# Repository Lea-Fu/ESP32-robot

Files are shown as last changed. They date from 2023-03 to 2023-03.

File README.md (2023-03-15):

# Autonomous tangible microrobots for app based (board) games

[Allgemein](#allgemein) <br>
[Tests](#tests) <br>
[Architekturüberlegung](#architekturüberlegung) <br>
[Implementierung](#implementierung) <br>
[Löten](#löten) <br>
[Steuerung](#steuerung) <br>
[Modellierung](#modellierung) <br>
[Display](#display) <br>
[Kamera](#kamera) <br>
[Nachrichten](#nachrichten) <br>
[App](#app) <br>
[Aruco Generation](#arucogeneration) <br>
[Ausblick](#ausblick) <br>

**Roboter:**
besteht aus: 
- ESP32(Wifi und Bluetooth) mit Kamera
- OLED Display
- H Brücke
- 2 Motoren N20 (2-4V 145RPM)
- Akku 3,7V 800mAh lipo
- 4 3D gedruckten Rädern
- 3D gedrucktes Getriebe
- 3D gedrucktes Gehäuse

**Gearbeitet wurde mit:**
- Für die **App**: Android Studio -> **Java**
- Für den **Roboter**: **PlatformIO** -> Arduino -> CLion -> **C++**
- Für die **Bildverarbeitung**: Computervision Bibliothek für ArUco Marker -> **OpenCV**
- Für das **Spielfeld**: um ein ArUco Board zu generieren -> OpenCV und **Python**
- Für die **Konstruktion** des Roboters: um die 3D Teile für den Roboter zu drucken -> **Fusion360** und **3D Drucker**

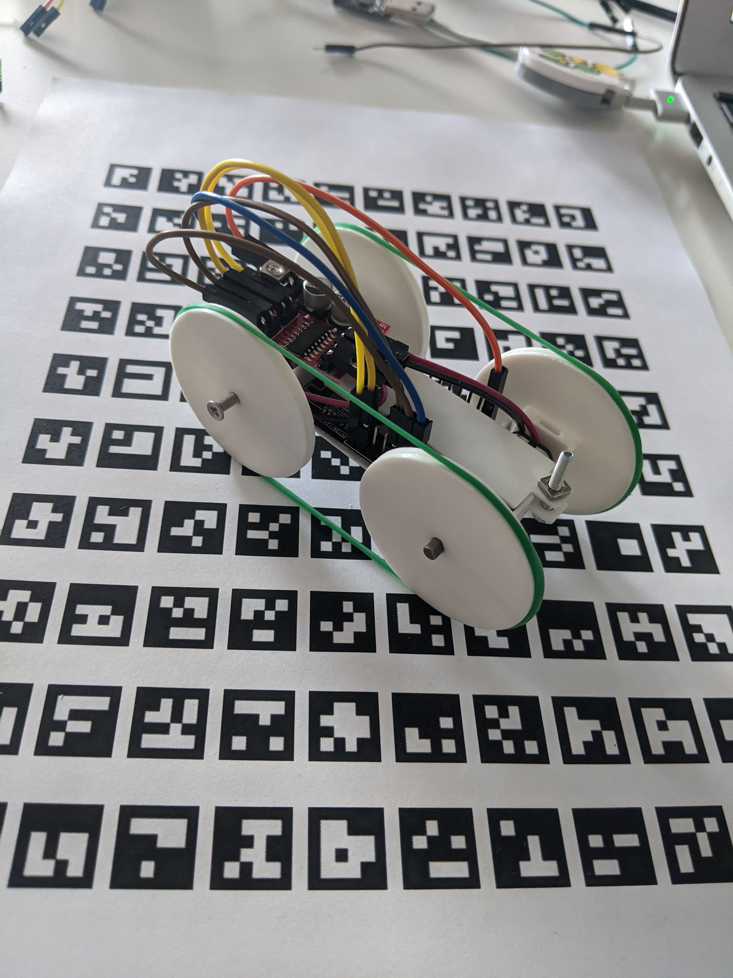
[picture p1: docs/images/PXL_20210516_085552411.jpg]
image of robot


App Icon (ganz oben links sieht man den Icon der App):
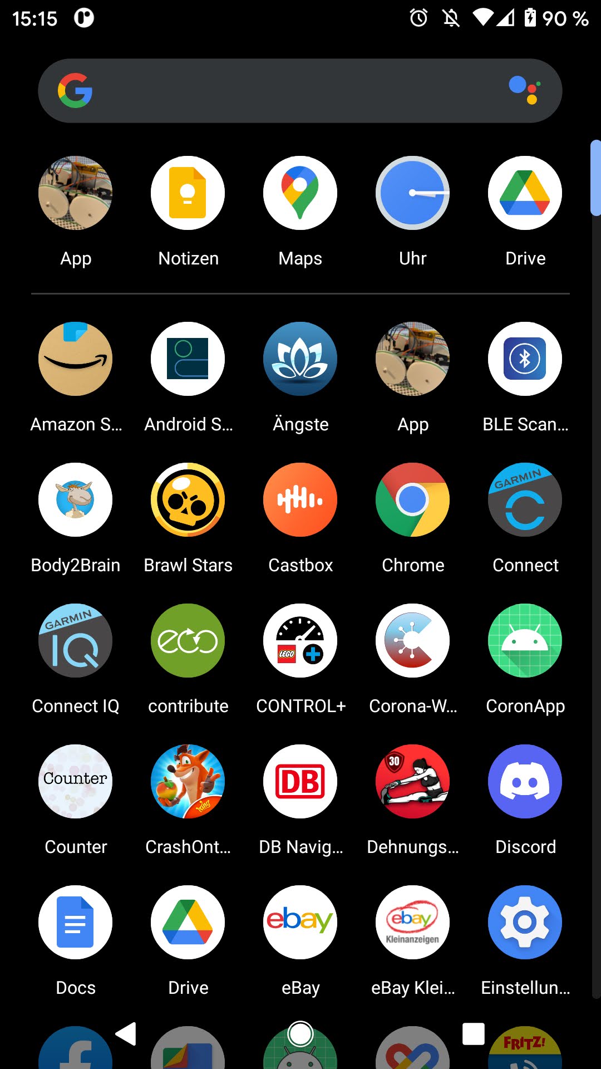
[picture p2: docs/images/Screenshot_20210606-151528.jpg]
image of app icon


## Erste Tests des ESP32

Nach Ankunft des **ESP32** mit Kamera testeten wir ihn, indem wir in **CLion** das Plugin für **PlatformIO** installierten. Um in CLion mit **Arduino** und dem esp32cam board arbeiten zu können, muss es unter  AI Thinker ausgewählt werden.

Das erste kleine Testprojekt besteht aus drei Teilen.
1. Ausgabe von "Hello" auf der Commandozeile
2. Anzeigen der verfügbaren WLAN Netzwerke
3. Möglichkeit des verbindens mit Bluetooth

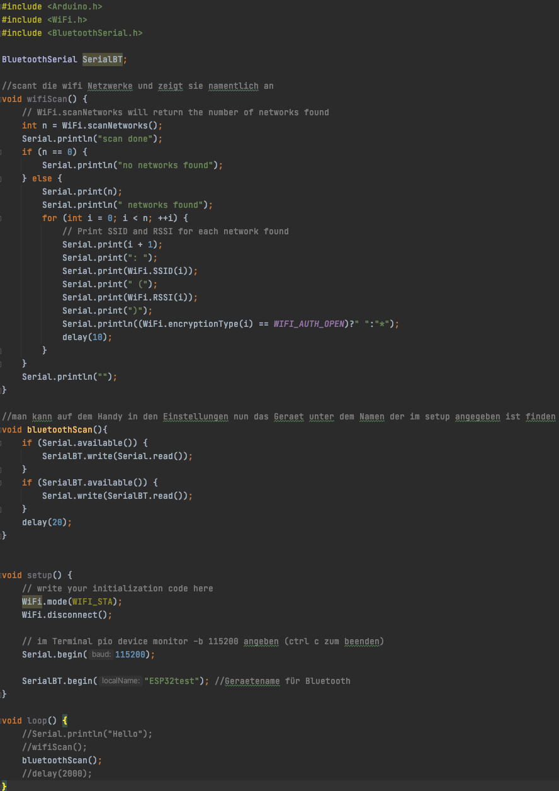
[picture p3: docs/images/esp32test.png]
esp32test code sample


## Architekturüberlegung

Sehr abstrakt gesehen:

architecturAbstrakt

Lose Kopplung -> hoher innerer Zusammenhalt und trennen der Zuständigkeiten

alles spezielle wegkapseln, damit es leicht austauschbar ist!

Erste Überlegungen zur "genauen" Architektur:

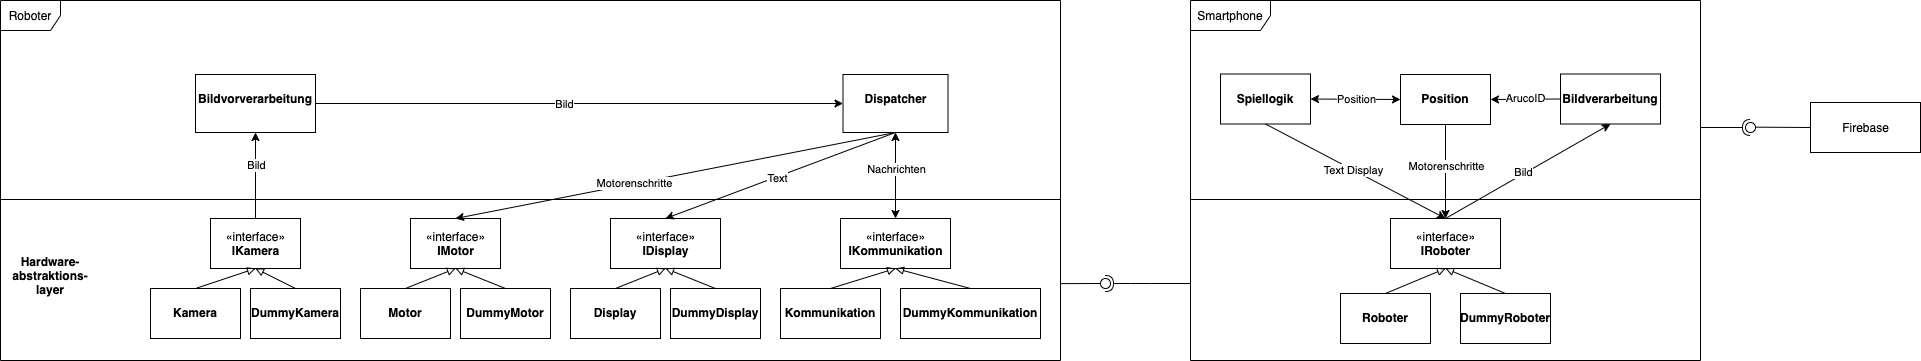
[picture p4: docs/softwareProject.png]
softwareProject


Auf der Seite der App war die Architekturüberlegung die im Diagramm zu sehen ist noch nicht genau genug und wurde deshalb nicht komplett übernommen. Auf Seite des Roboters hat es bis zum Ende hin gepasst und die Architektur vom Anfang wurde übernommen.

Für die Klasse dispatcher auf dem Roboter:

| Komponente | Feld 0 | Feld 1 |
| --- | --- | --- |
| Format | Header 1 Byte Adresse für HAL Komponenten | Nachricht |
| Kamera | '0' | ‘0‘ für senden der graustufen Bilder ‘1‘ für stop |
| Motor1 | '1' | message[1]'1' oder '0' für Vorwärts oder Rückwärts, oder '2' für stop, als String, alles andere um nichts zu tun |
| Motor2 | '1' | message[2]'1' oder '0' für Vorwärts oder Rückwärts, oder '2' für stop, als String, alles andere um nichts zu tun |
| Display | '3' | Text als String |

## Implementierung für den Roboter

Es wurde sich als Konvention für "snake case" entschieden. Also alles wird mit Unterstrichen (_) getrennt.

Die Klassen sind, wie unter [Architekturüberlegung](#architekturüberlegung) festgehalten, eingeteilt. Zu jeder .cpp File gibt es eine passende .h File. Die Header liegen alle im "include" Ordner. In diesem befindet sich der Unterordner "hal", dies steht für HardwareAbstraktionsLayer. Die Source Files liegen alle im "src" Ordner und auch hier gibt es den Unterordner "hal".
"i" am Anfang eines Klassennamen deutet auf ein Interface hin.

Struktur:
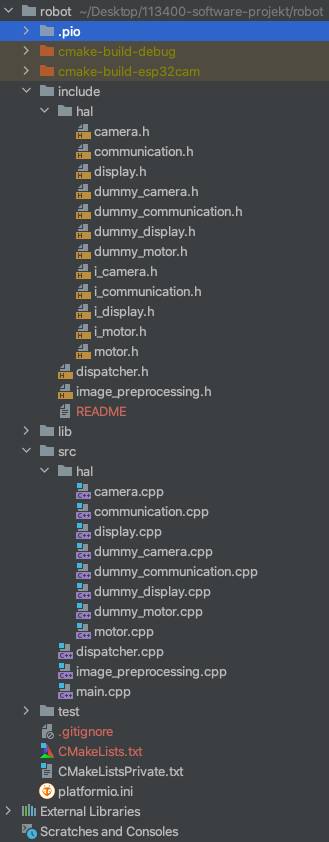
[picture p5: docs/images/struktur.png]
struktur


1. Zuerst wurde die WLAN und Bluetooth Funktionalität aus den ersten Tests des ESPs hier in die communication eingebunden.
2. Als nächstes wurde start und stop für den Motor implementiert. Siehe unter [Steuerung](#steuerung)
3. Dann wurde der dispatcher für das senden und empfangen von Nachrichten implementiert.
4. Implementierung für das Display zum Anzeigen von Nachrichten. Siehe unter [Display](#display)
5. Die Kamera kann nun ein Foto aufnehmen. Siehe unter [Kamera](#kamera)
6. Nachrichten über BLE (Bluetooth Low Energy) senden. Problem: wir bekommen mit einem normalen Netzteil 4,7 V und das reicht nicht. Also der Brownout detector springt an, da es einen Spannungsabfall gibt. Lösung: Kondensator reicht nicht, also stärkeres Netzteil. Selbst 9,6 V haben nicht funktioniert. Also haben wir einfach einen neuen ESP32 benutzt. Es ging sofort, nur mit dem Strom des Laptops ohne Probleme. Siehe unter [Nachrichten](#nachrichten)
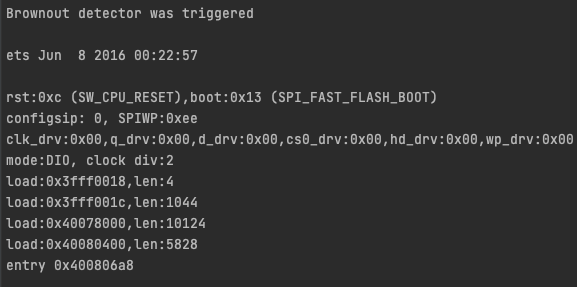
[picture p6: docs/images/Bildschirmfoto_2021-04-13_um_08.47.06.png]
Bildschirmfoto_2021-04-13_um_08.47.06


7. über BLE ein Bild vom ESP32 an die inzwischen selbst geschriebene App schicken. Problem: Bild ist 9,216KB groß, ESP sendet nur bis 0,6KB. Lösung: Paket in Packages aufteilen und rüberschicken.
8. das Bild enthält einen Marker der mittels OpenCV erkannt wird. So weiß der Roboter wo er ist und wo er hin muss.

## Löten von Motoren und H Brücke

Zuerst braucht man den Lötkolben, eine dritte Hand, Lötzinn, Kabel, Motoren und die H-Brücke.
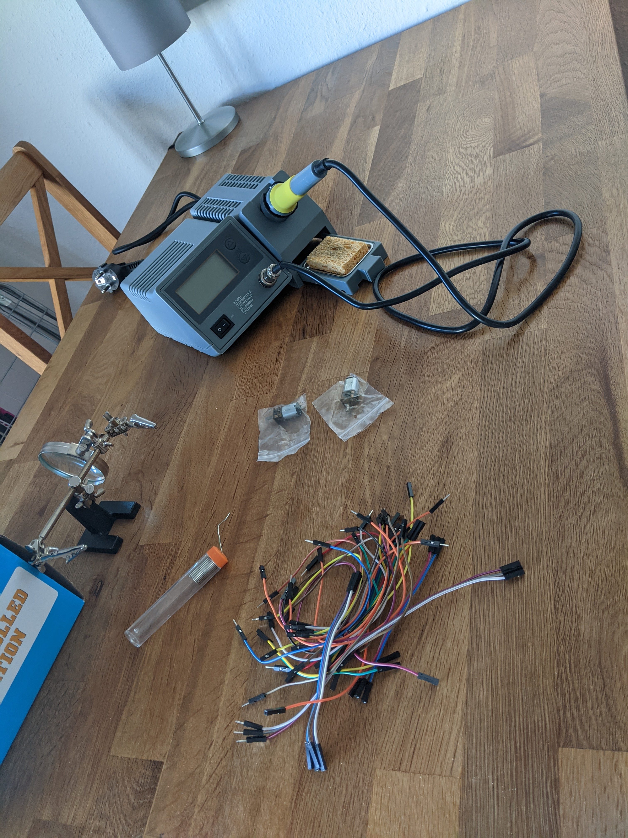
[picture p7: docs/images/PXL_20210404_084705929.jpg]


Dann nimmt man sich zwei Motoren und 2 Kabel (female auf beiden Seiten).
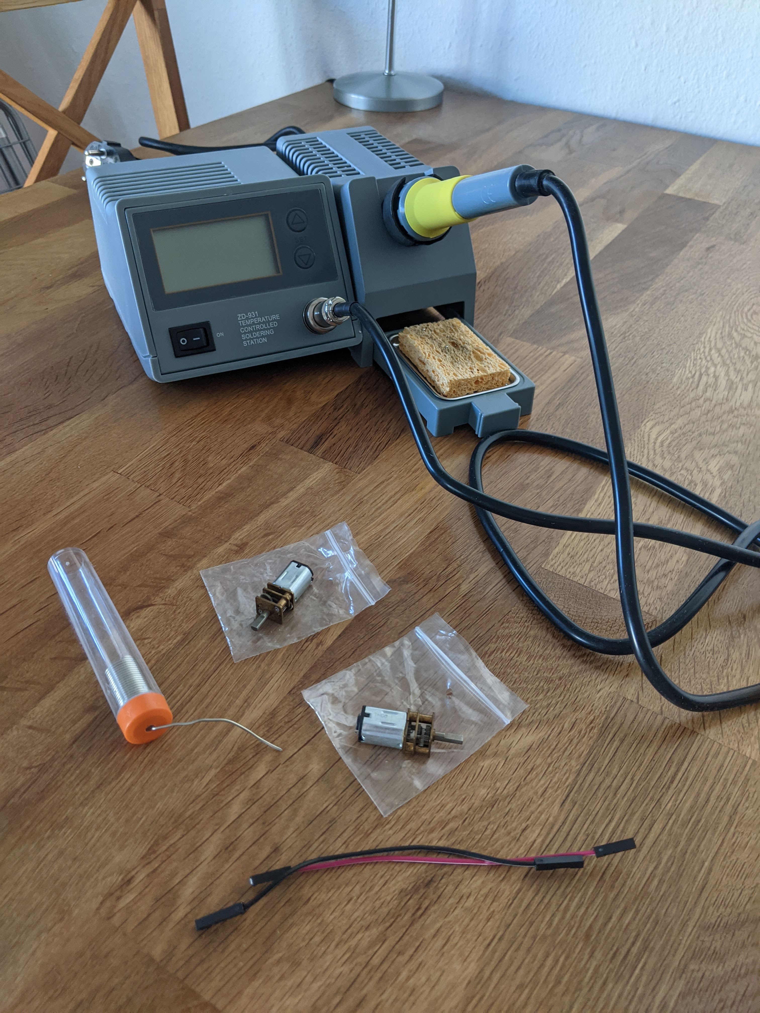
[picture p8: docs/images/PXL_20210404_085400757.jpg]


Nun trennt man beide Kabel genau in der Mitte und entfernt die Isolierung vorsichtig.
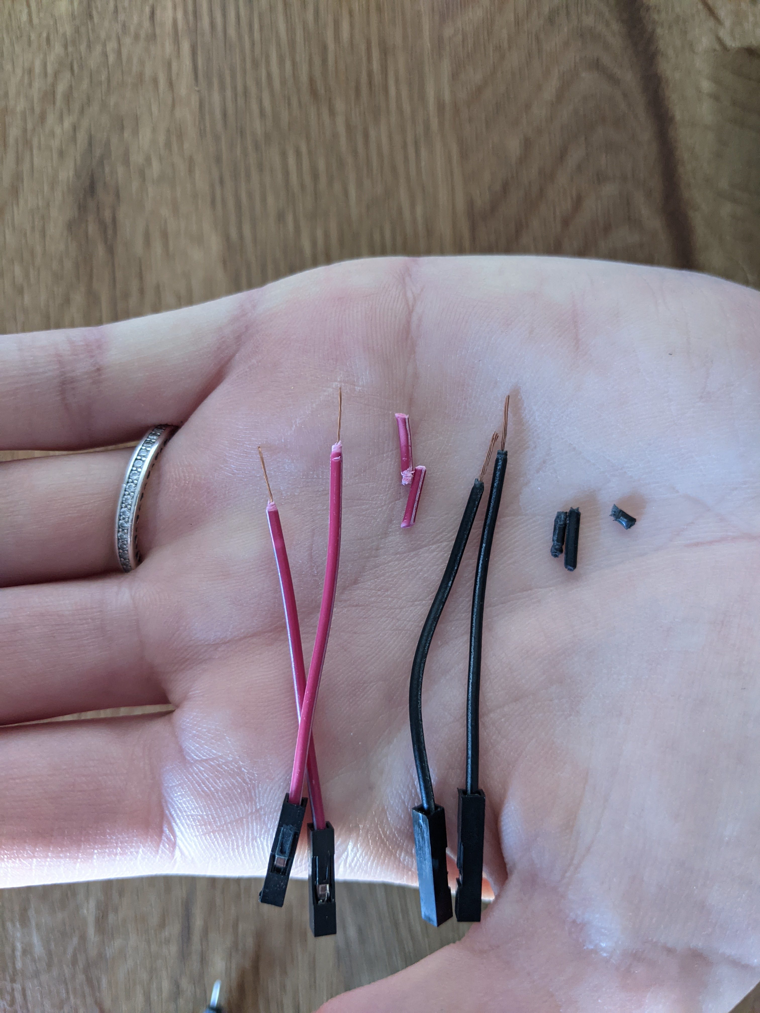
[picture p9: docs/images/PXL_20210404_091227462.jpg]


Wir haben uns für rot als Plus- und schwarz als Minus-Kabel entschieden. Die Kabel können nun an die Motoren gelötet werden.
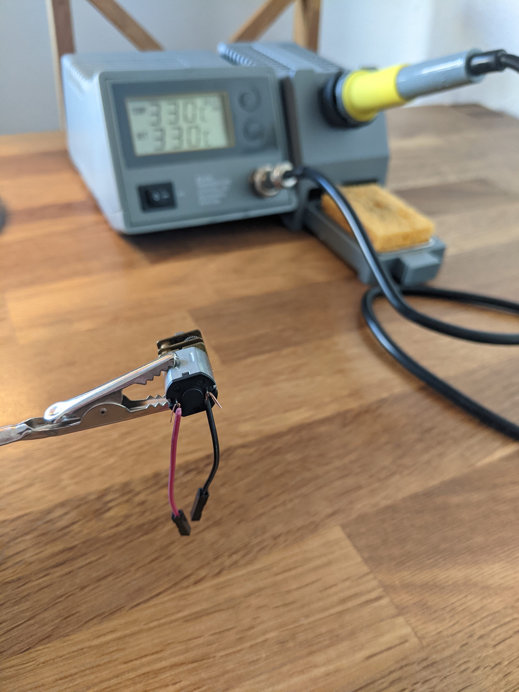
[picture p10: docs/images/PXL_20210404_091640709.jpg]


Man kann den Motor nun mit rot an 3,3V und mit schwarz an G für Ground des ESP stecken. Dies haben wir zum testen gemacht. Wenn man den ESP nun mit der Steckdose verbindet, läuft der Motor.
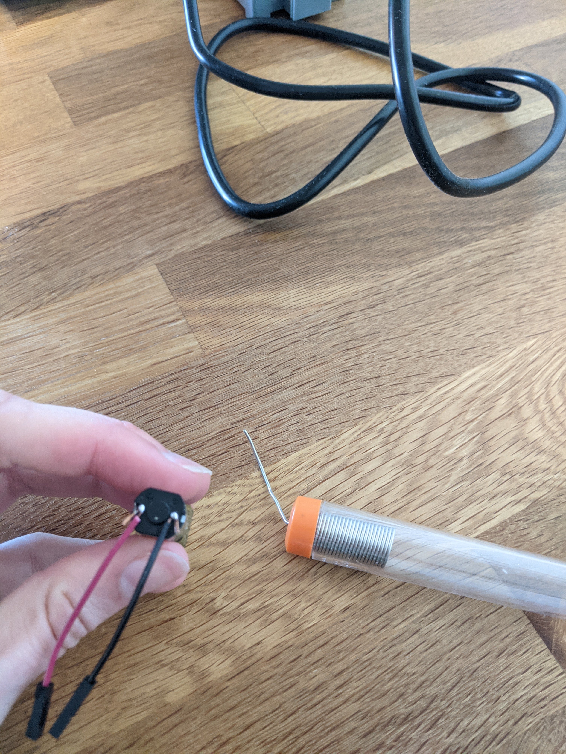
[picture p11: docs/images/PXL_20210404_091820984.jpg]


Dann trennt man immer zwei Kontaktstifte von der Stiftleiste ab. 5 Paare werden für eine H-Brücke gebraucht.
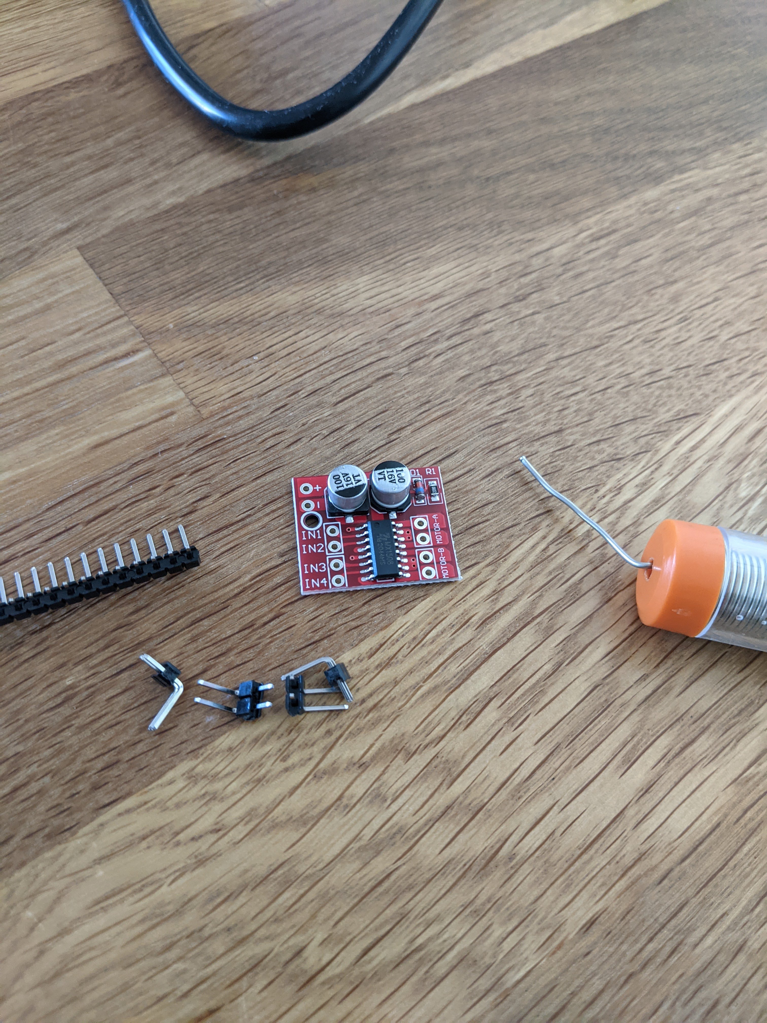
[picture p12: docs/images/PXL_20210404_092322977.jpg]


Diese lötet man nun fest.
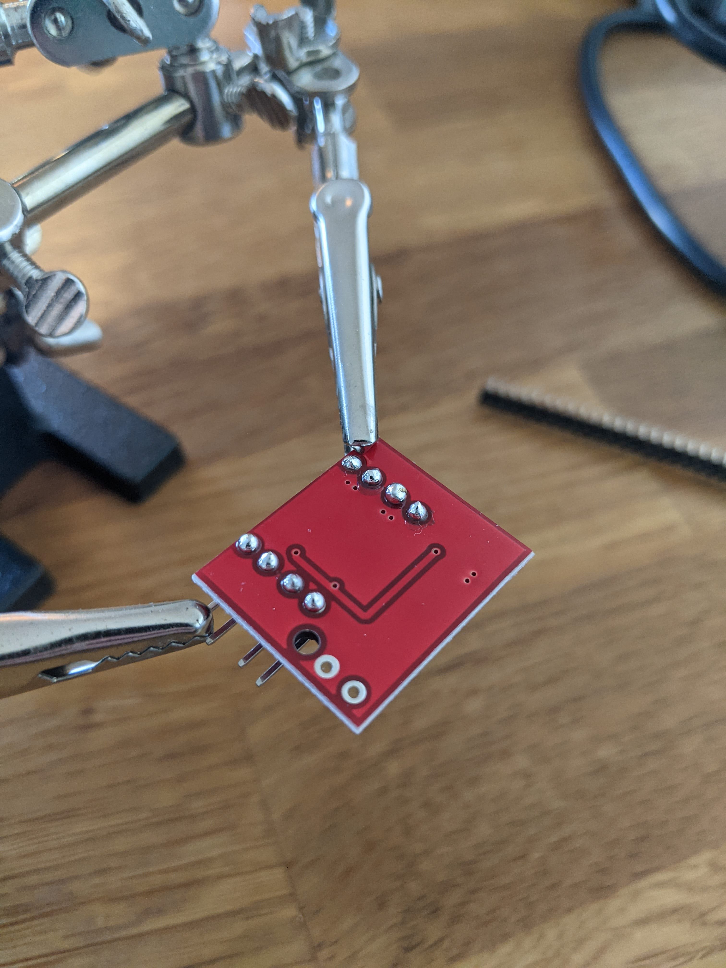
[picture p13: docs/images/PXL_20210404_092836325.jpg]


Hier sind alle festgelötet.
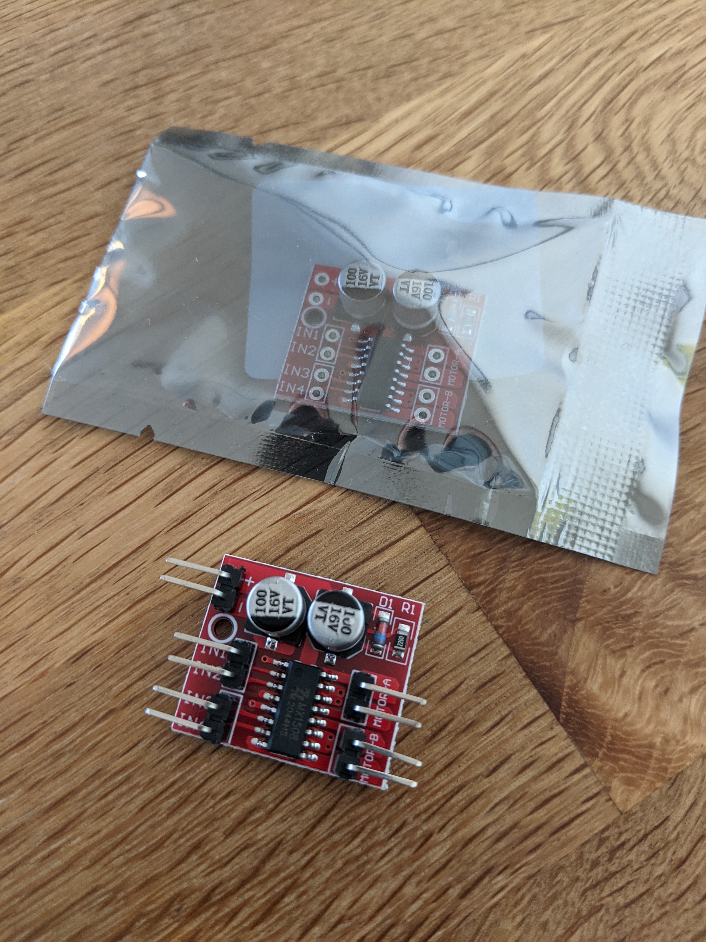
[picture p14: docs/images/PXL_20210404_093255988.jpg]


Man kann die Motoren nun an Motor A und Motor B der H-Brücke befestigen.
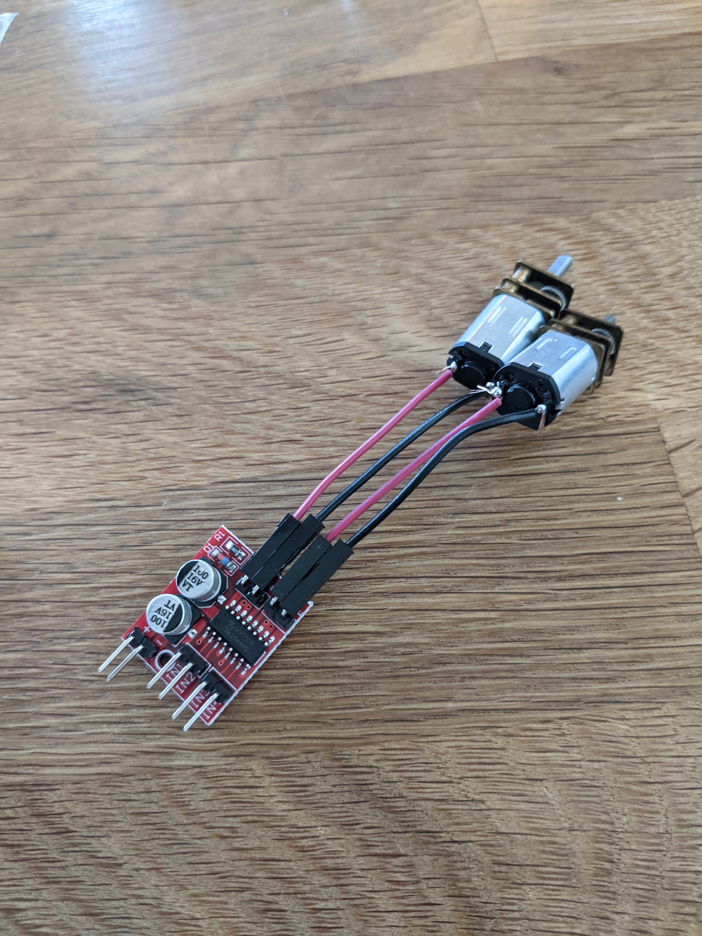
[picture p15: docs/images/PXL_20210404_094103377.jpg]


## Motoren ansteuern

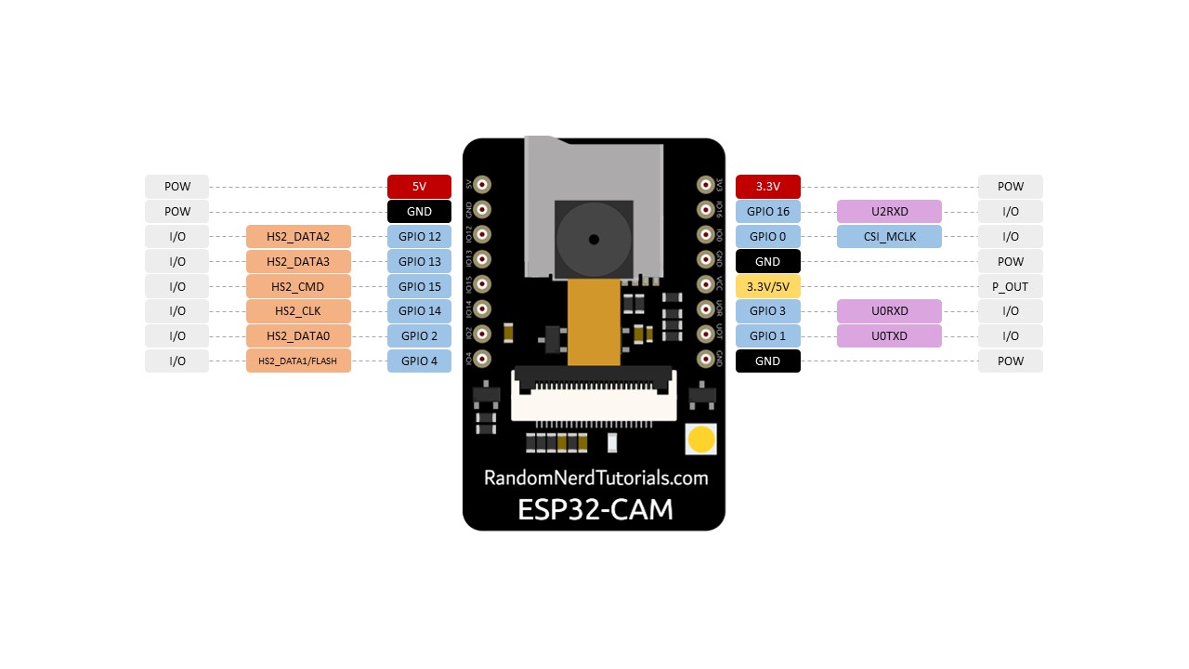
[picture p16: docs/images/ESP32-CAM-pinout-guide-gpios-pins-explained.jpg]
ESP32-CAM-pinout-guide-gpios-pins-explained


Um zu gucken, welche Pins des ESP32 auf welche in Arduino gemappt sind.

https://randomnerdtutorials.com/esp32-cam-ai-thinker-pinout/

Aufbau zum Testen:

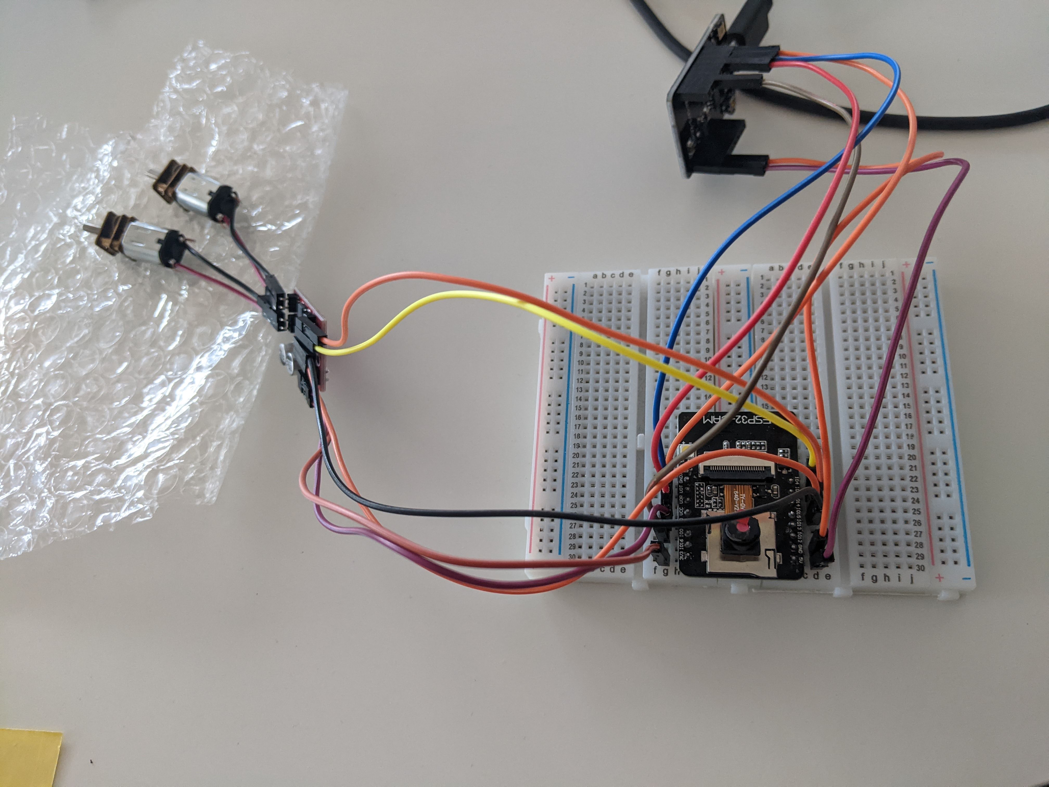
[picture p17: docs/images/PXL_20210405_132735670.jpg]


Die beiden Motoren werden an die H-Brücke angeschlossen.
Die H-Brücke wird mit Motor A an IO13 und IO12 angeschlossen. Motor B wird an IO4 und IO2 angeschlossen. Plus der H-Brücke wird an 3,3V und Minus der H-Brücke an GRN (Ground).
5V des ESP32 wird an 5V des Adapters für den Strom angeschlossen und GND (Ground) des ESP32 wird an GND (Ground) des Adapters für den Strom angeschlossen.

Zusätzlich habe ich noch IO0, UOR, UOT, GND/R an die jeweiligen Pins des Adapter angeschlossen, um den Code uploaden zu können, ohne des ESP32 von der Steckplatte nehmen zu müssen.

IO4 musste gegen IO14 ersetzt werden, da die LED an IO4 hängt und somit immer an geht, wenn man den Motor anspricht. Da wir nun PVM für die Motoren benutzen, um die Geschwindigkeit zu steuern, flackert die LED, so können die Marker nicht mehr erkannt werden. Deswegen musste der Pin gewechselt werden, das bedeutet aber auch, das nicht genug freie Pins für das Display vorhanden ist und dies wegfallen muss.

## Modellierung in Fusion360

Der Roboter wird in Fusion360 modelliert, um die Basis und die Räder 3D Drucken zu können.

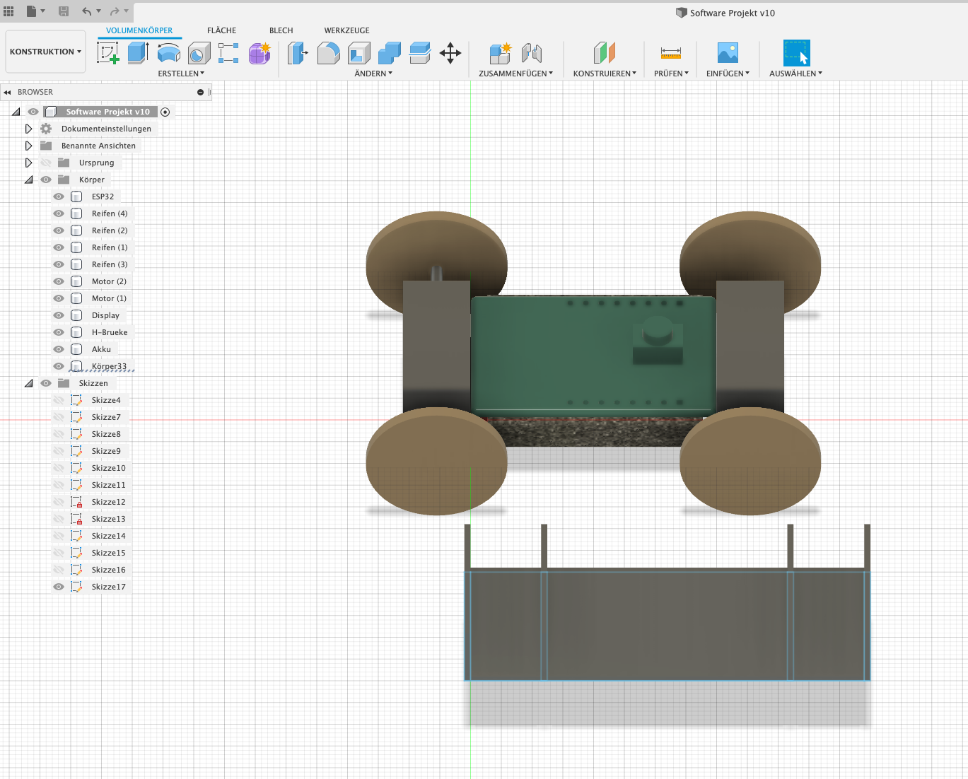
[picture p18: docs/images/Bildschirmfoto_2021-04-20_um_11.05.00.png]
Bildschirmfoto_2021-04-20_um_11.05.00


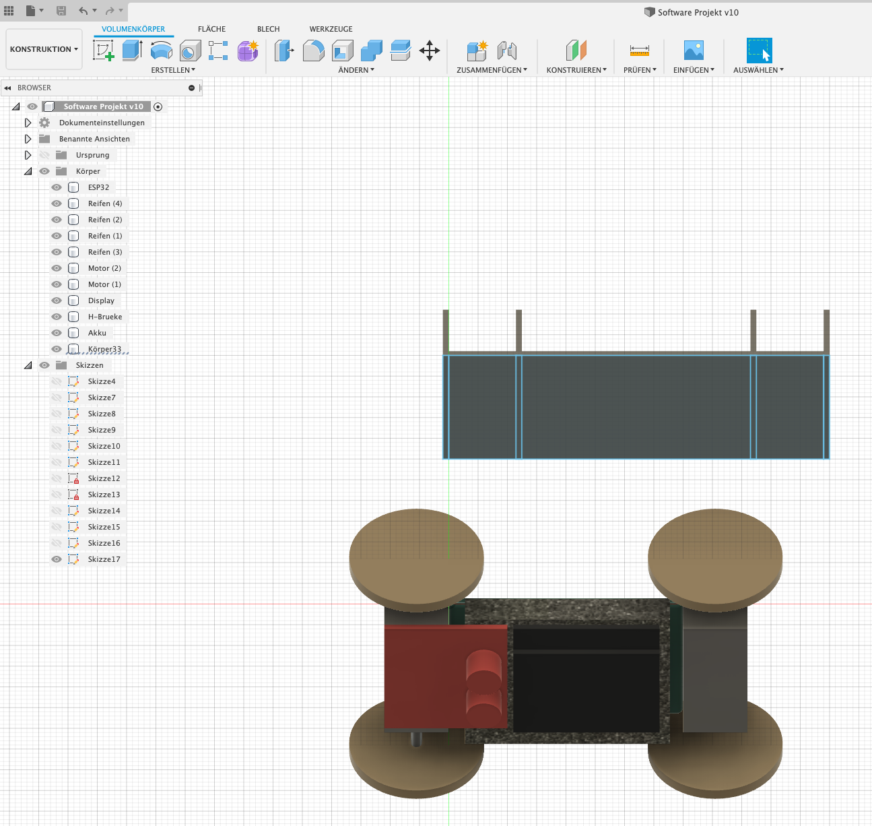
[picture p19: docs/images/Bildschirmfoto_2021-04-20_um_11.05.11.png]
Bildschirmfoto_2021-04-20_um_11.05.11


Hier sieht man erste Prototypen.

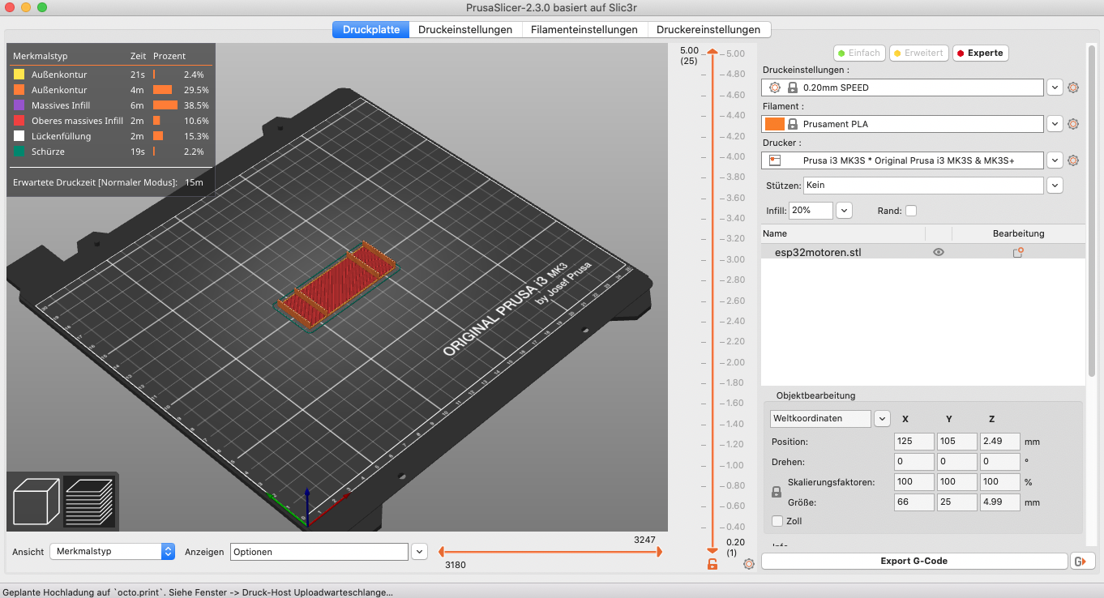
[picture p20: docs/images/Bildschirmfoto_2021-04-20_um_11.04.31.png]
Bildschirmfoto_2021-04-20_um_11.04.31


Dies ist der erste Testdruck für die Halterung des ESP32 und der Motoren, die rechts und links daneben kommen.

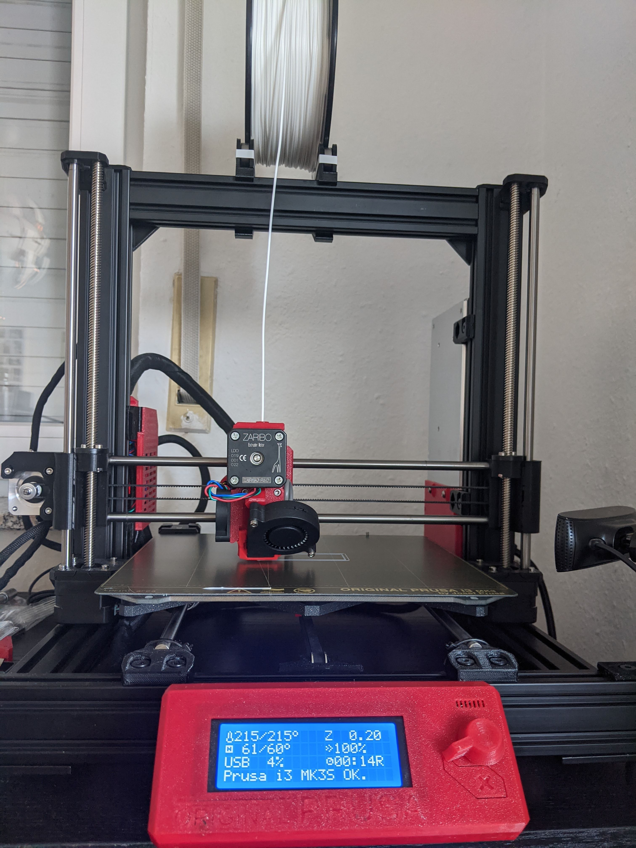
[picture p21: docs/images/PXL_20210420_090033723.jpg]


Hier der erste fertige Testdruck. Die Toleranzen werden nun weiter überarbeitet, bis es perfekt passt.

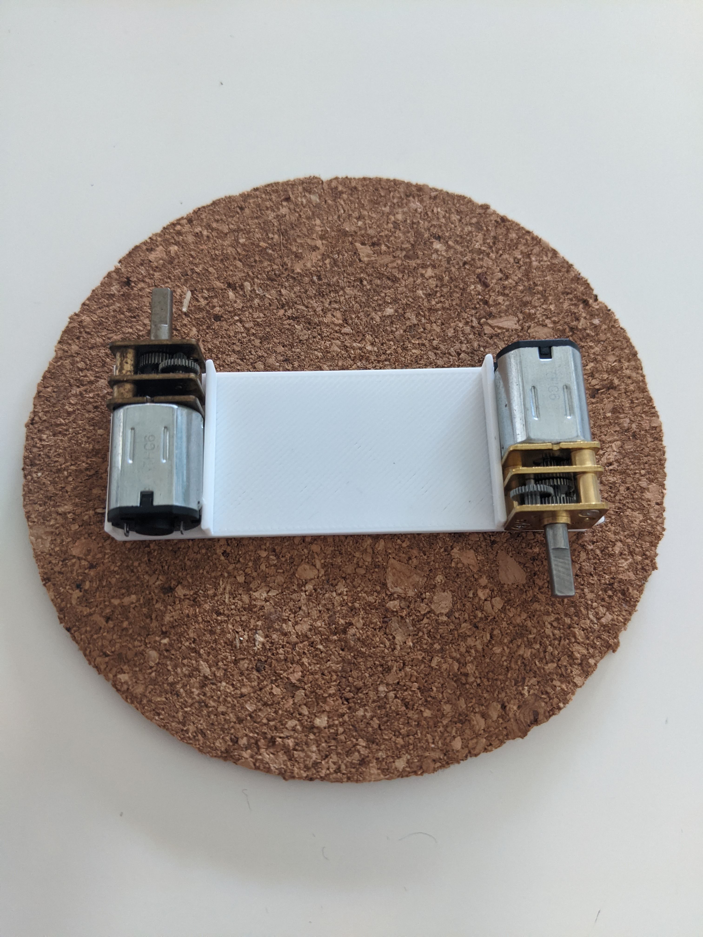
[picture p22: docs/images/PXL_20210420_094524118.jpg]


Der Wendepunkt liegt genau in der Mitte, damit ist der **Roboter** im Gegensatz zu einem Auto **Holonom** und kann sich **auf der Stelle drehen**, indem ein Motor vorwärts, der andere rückwärts fährt.

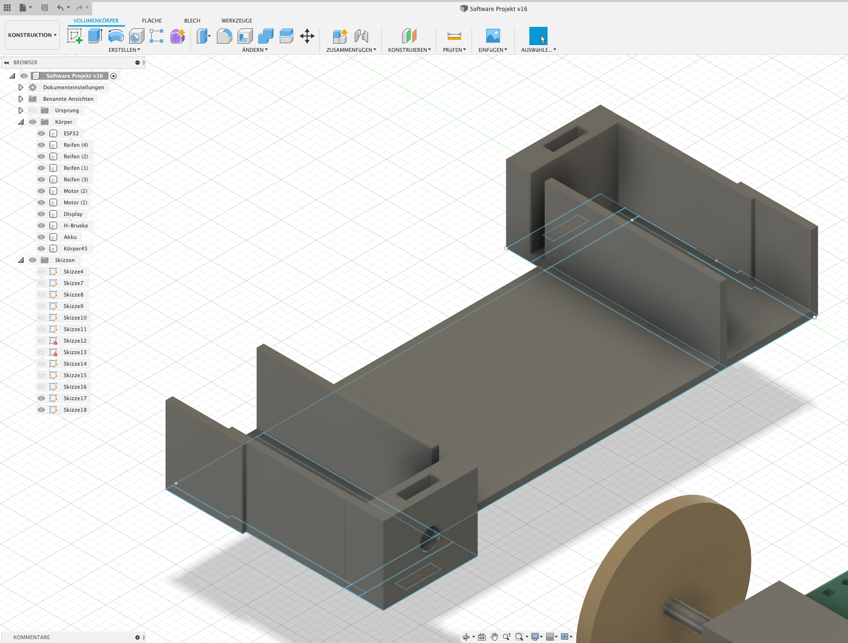
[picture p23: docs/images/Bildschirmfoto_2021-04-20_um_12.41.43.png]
Bildschirmfoto_2021-04-20_um_12.41.43


Hier sind hinter den Motoren nun Wände, zwischen diesen müssen die Kabel langgehen und in den Wänden ist Platz für eine M2,5 4Kant Mutter. In die kommt eine Schraube M2,5 x 12, an diese soll dann das Rad.

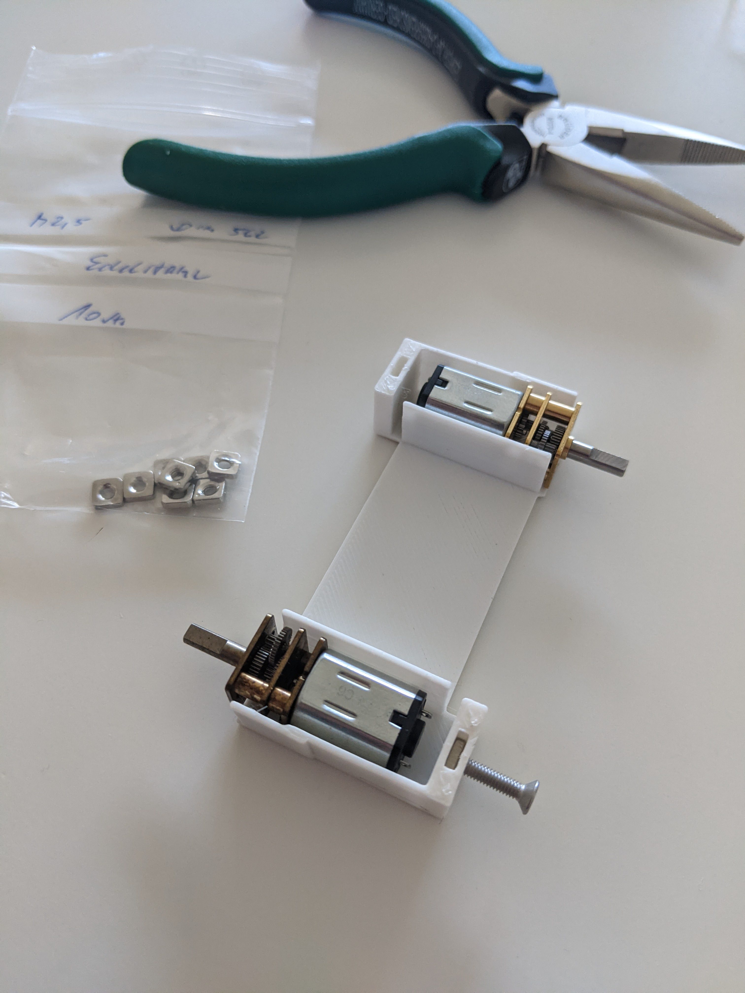
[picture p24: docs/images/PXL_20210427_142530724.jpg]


Hier sind die zwei Motoren und der Esp32 cam verbaut. Es fehlt also oben noch der Akku, das Display und die H-Brücke muss auch noch drauf.

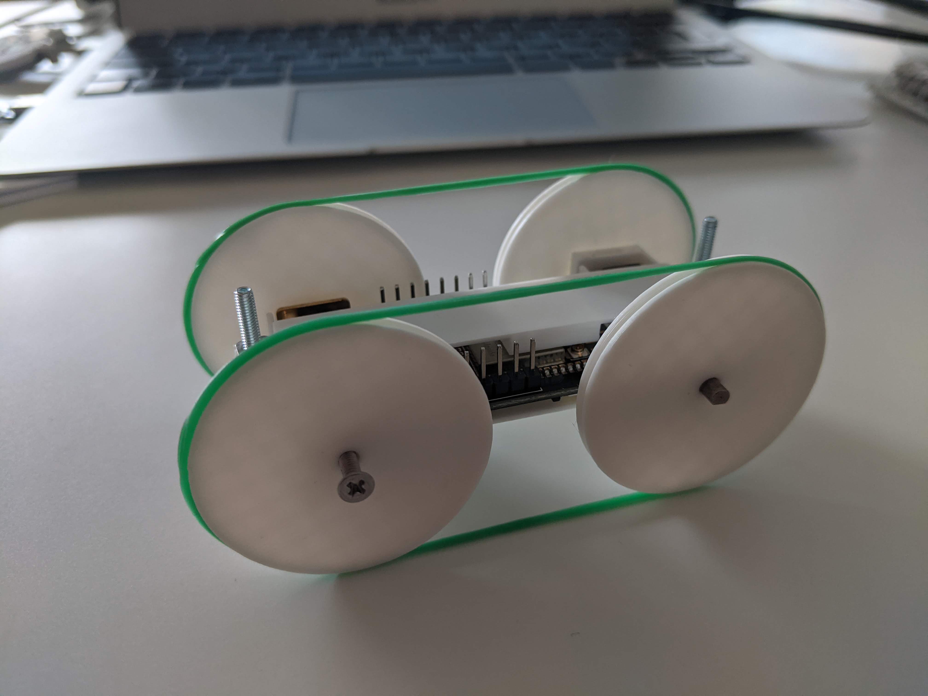
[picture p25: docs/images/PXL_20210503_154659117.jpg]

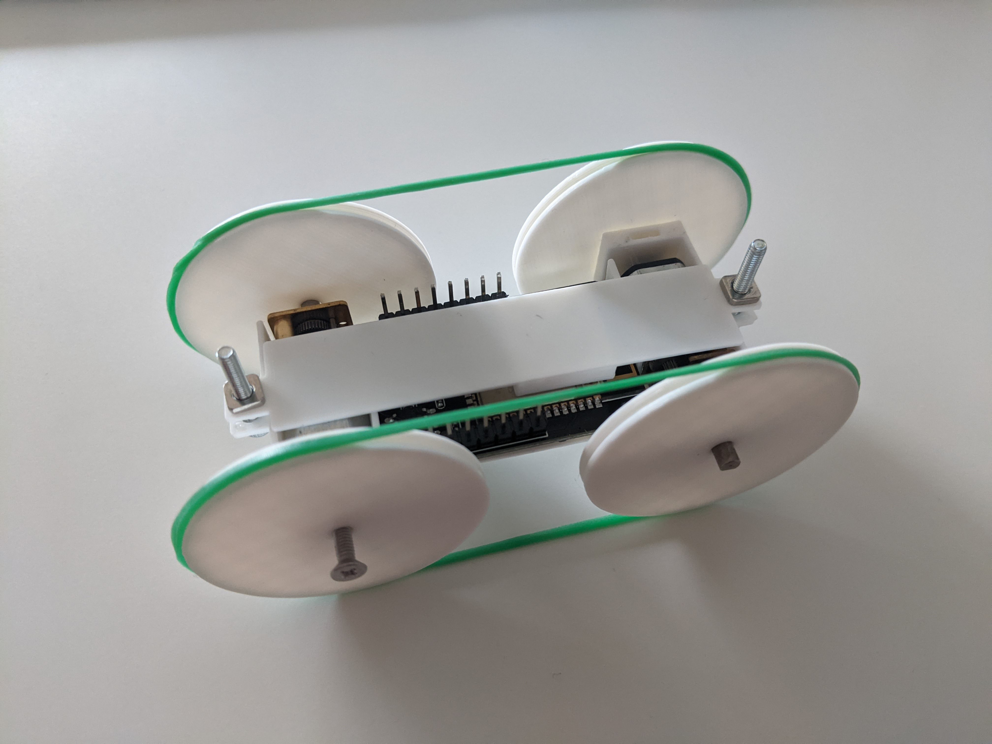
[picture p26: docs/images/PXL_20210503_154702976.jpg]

Auf dem folgenden Bild sieht man den Robo von unten. Hier sieht man die Kamera, die die ArUco Marker auf den Feldern erkennt. Wir benutzen sie, damit wir wissen, auf welchem Feld wir stehen (Marker ID -> x und y Koordinate) und wie wir allgemein stehen (Pose estimation -> Translation und Rotation zum Marker):
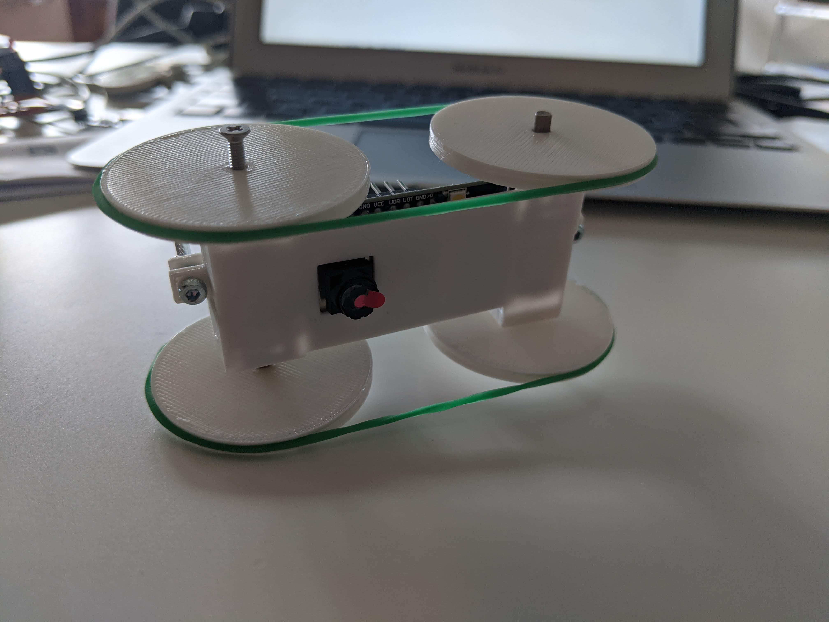
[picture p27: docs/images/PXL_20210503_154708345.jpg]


Der Roboter zusammengebaut:


Drucken größerer Reifen:
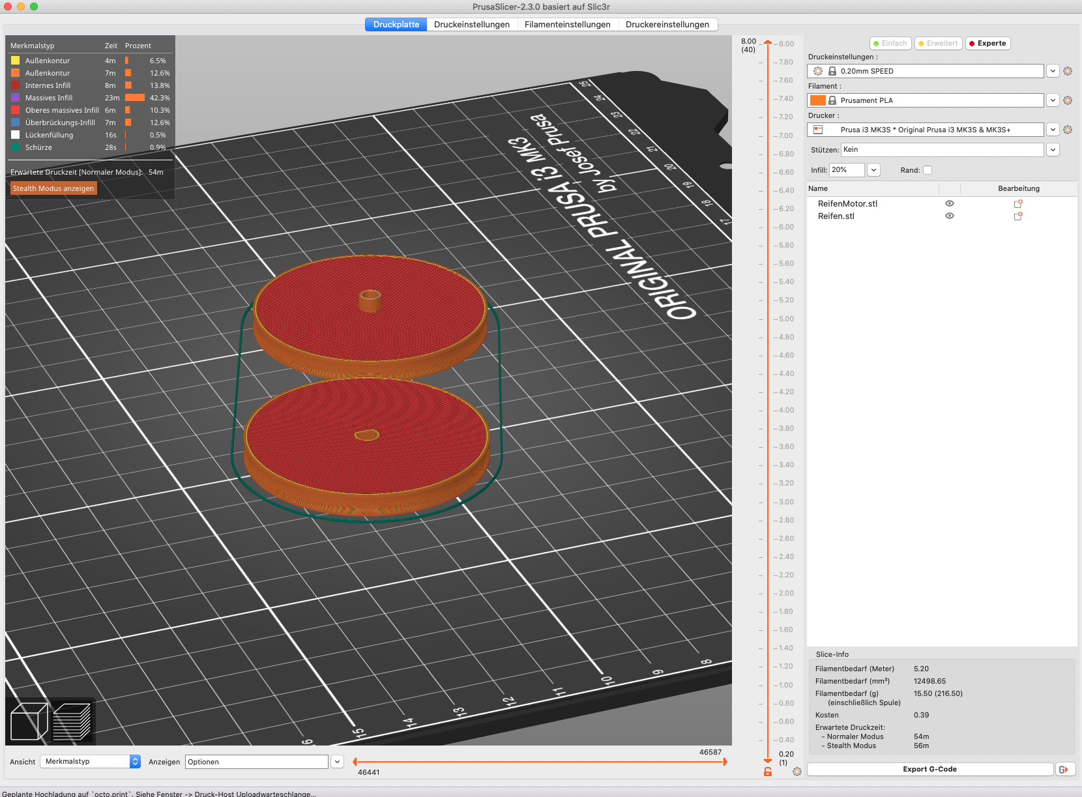
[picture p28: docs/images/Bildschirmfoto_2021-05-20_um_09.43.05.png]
Bildschirmfoto_2021-05-20_um_09.43.05


Um den Roboter zusammenzubauen braucht man die .stl Files aus dem Repo. Sie liegen auf dem Master Branch unter docs/CAD.

## Display testen

Bibliothek für das Display: 
https://platformio.org/lib/show/135/Adafruit%20SSD1306/examples
https://platformio.org/lib/show/6214/Adafruit%20BusIO/installation

Das Display hat GND, das muss an GND vom ESP32 angeschlossen werden. 
VCC vom Display wird an 3,3V vom ESP32 angeschlossen. 
SCL wird an IO15 und SDA an IO14 angeschlossen.

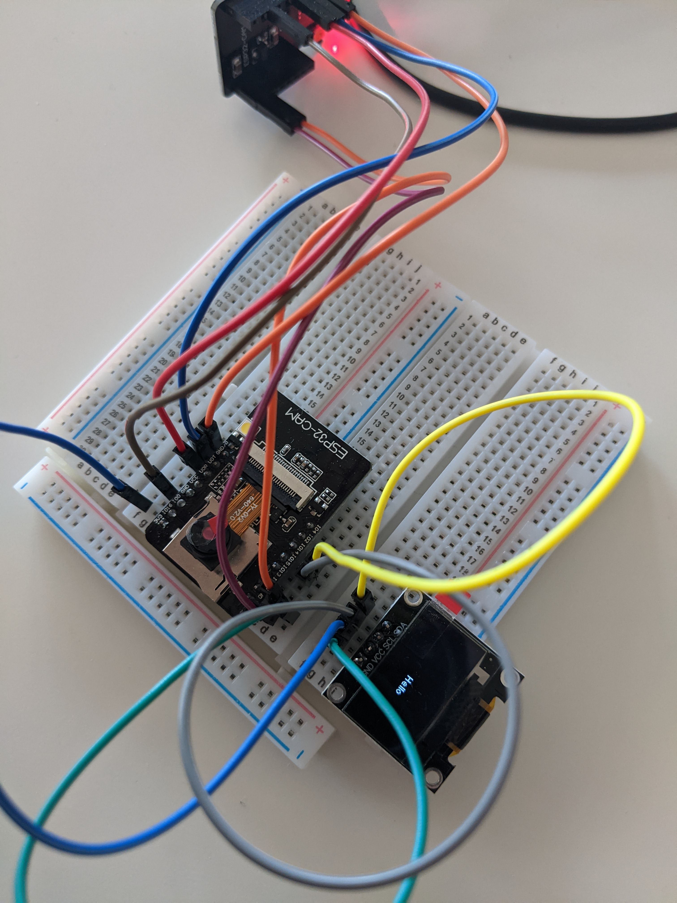
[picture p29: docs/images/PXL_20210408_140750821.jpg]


Das Display konnte im fertigen Projekt nicht mehr integriert werden, da der ESP zu wenige Pins besitzt. Dem Motor mussten leider ein Display Pin geben werden, wegen der LED des ESP. Mehr dazu siehe [steuerung](#steuerung).

## Kamera testen

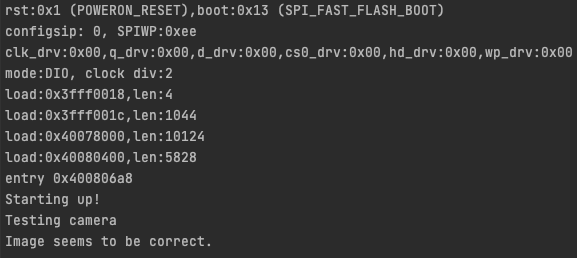
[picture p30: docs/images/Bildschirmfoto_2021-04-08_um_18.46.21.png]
Bildschirmfoto_2021-04-08_um_18.46.21


Unter dem Punkt die App kann man sehen, das die aufgenommenen Bilder 9,216 KB groß sind. Diese werden in 19 Paketen vom ESP32 zur App gesendet.

Mit der Nachricht "00" fängt er an Bilder zu senden. So schnell er kann. Es sieht aus, wie ein flüssiges Video. Mit "01" stoppt man das ganze.

## Nachrichten senden

Man kann auf dem Handy eine App namens BLE Scanner installieren. Dort kann man sich mit dem ESP32 verbinden und eine Nachricht senden. Diese kann man dann im Terminal von C Lion sehen, wenn man "pio device monitor -b 115200" eingibt.

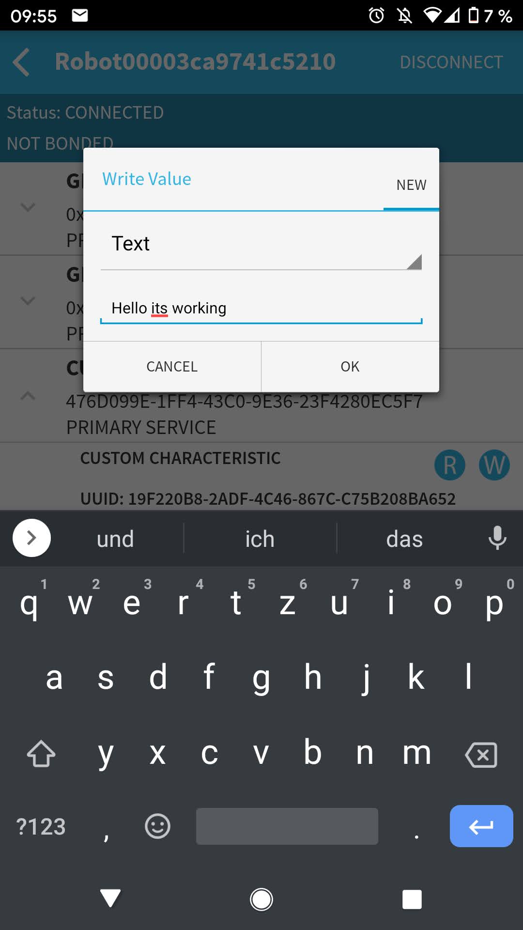
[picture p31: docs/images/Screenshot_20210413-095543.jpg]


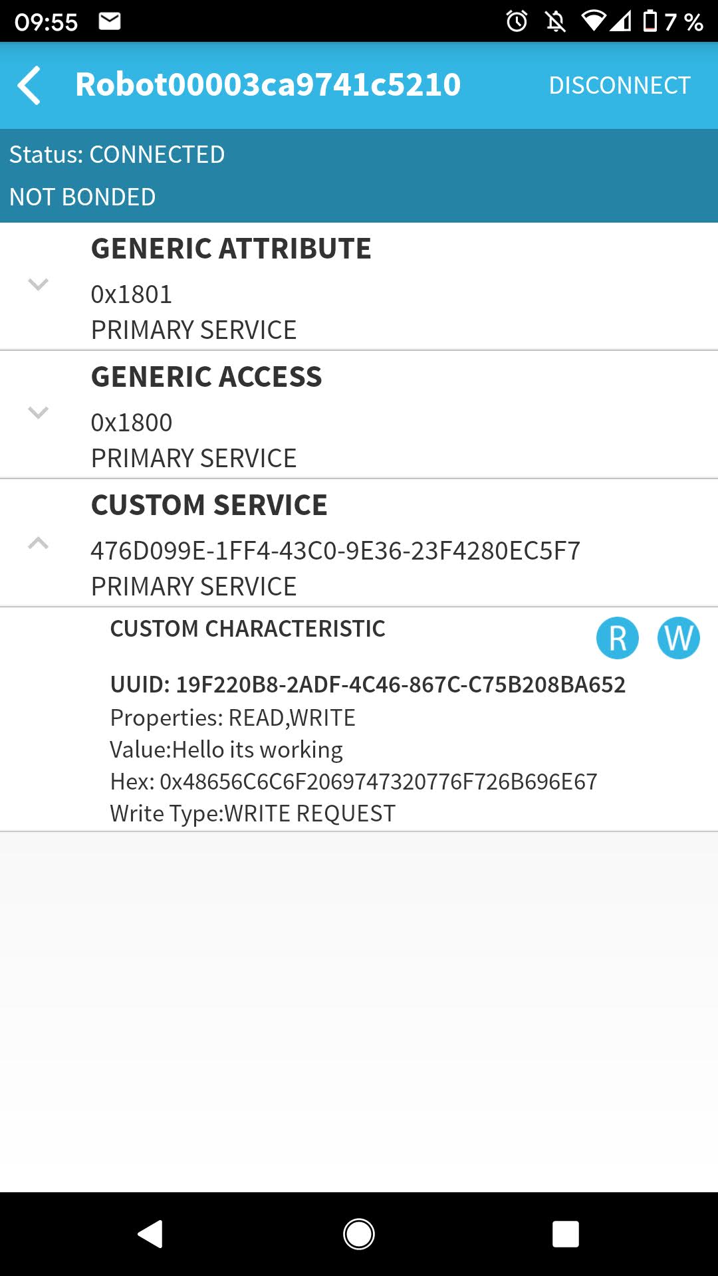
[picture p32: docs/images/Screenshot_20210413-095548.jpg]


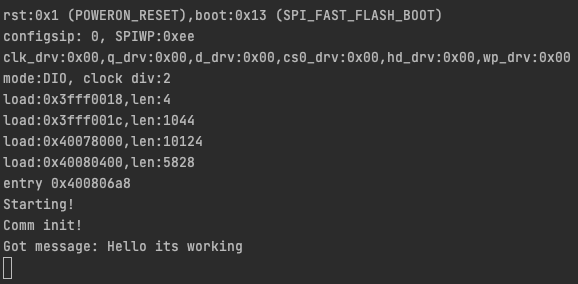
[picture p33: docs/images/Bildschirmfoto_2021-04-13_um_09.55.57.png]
Bildschirmfoto_2021-04-13_um_09.55.57


## Die App

OpenCV 4.5.2 mit contribs!!! für Android Studio: 

https://pullrequest.opencv.org/buildbot/export/opencv_releases/master-contrib_pack-contrib-android/20210425-042121--11332/

https://stackoverflow.com/questions/17767557/how-to-use-opencv-in-using-gradle

https://docs.opencv.org/2.4/doc/tutorials/introduction/android_binary_package/O4A_SDK.html

Wichtig:
https://stackoverflow.com/questions/57698796/cannot-detect-opencv-libs-after-update-form-3-4-3-to-4-1-1

Anfänglich:
1. Momentan kann man mit der App (auf dem Dev Branch Unterordner phone) über BLE mit dem Robo (ESP32) kommunizieren.
2. OpenCV ist über die oberen beiden Links mit eingebunden. Mit OpenCV können wir die ArUco Marker per Kamera erkennen.

https://docs.opencv.org/3.4.3/d5/dae/tutorial_aruco_detection.html

Hier wurde auf Papier der ArUco Marker mit der Id 7 ausgedruckt und vor die Kamera gehalten. Der Marker wird erkannt!

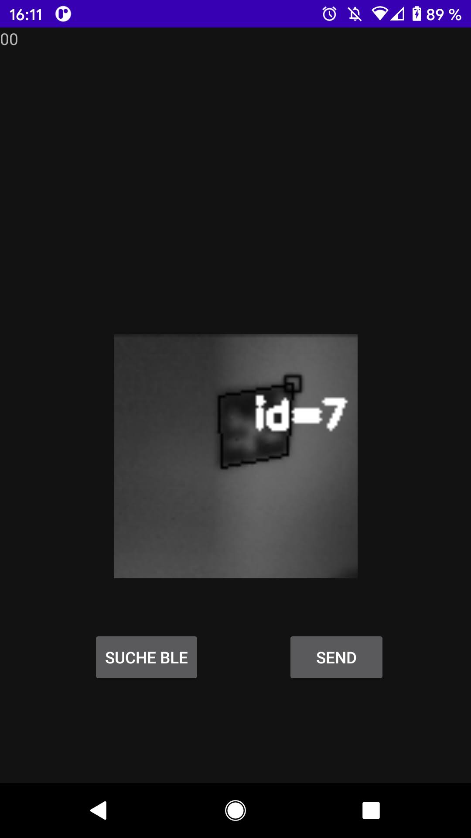
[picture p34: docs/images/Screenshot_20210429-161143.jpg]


_Stand Ende des Projekts:_

-Redesign der App
-Button zum Verbinden des Roboters über BLE
-Button zum senden einzelner Strings zum testen
-DropDown Menü um auszuwählen, zu welchem Feld der Roboter fahren soll.

Beim Fahren korrigiert er sich nach jedem Schritt durch die **Pose Estimation** selbst. Translation und Rotation werden berechnet. So weiß der Roboter auf welchem Feld er steht und mit welchem Winkel er zu den Markern steht. Durch diesen Winkel korrigiert er sich nach jedem Schritt selbst um immer "geradeaus" zu fahren oder sich zu drehen.

**ArUco Marker Erkennung**:
wenn kein Marker erkannt wird kann dies
- an dem Winkel in dem der Roboter zu ihm steht,
- oder dem **Rauschen der Kamera**,
- oder **Interferenzen der Motoren** (hierdurch evtl. verfälschte Bilddaten und verlorene Pakete),
- oder der geringen Auflösung der Kamera,
liegen.

Screenshot direkt nach dem Verbinden:
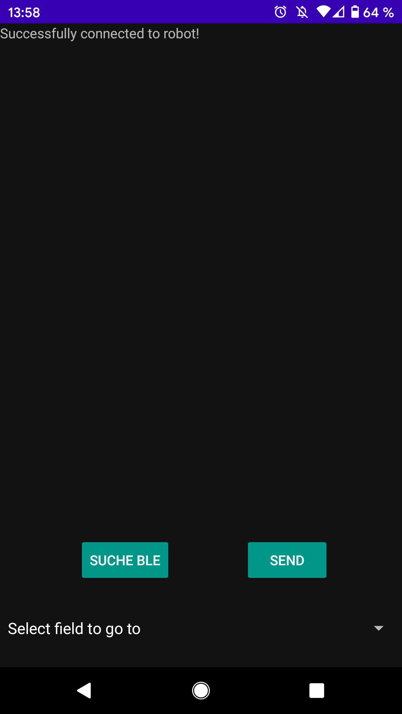
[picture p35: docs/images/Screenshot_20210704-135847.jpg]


Screenshot nach dem Klick auf eine ID im DropDown Menü:
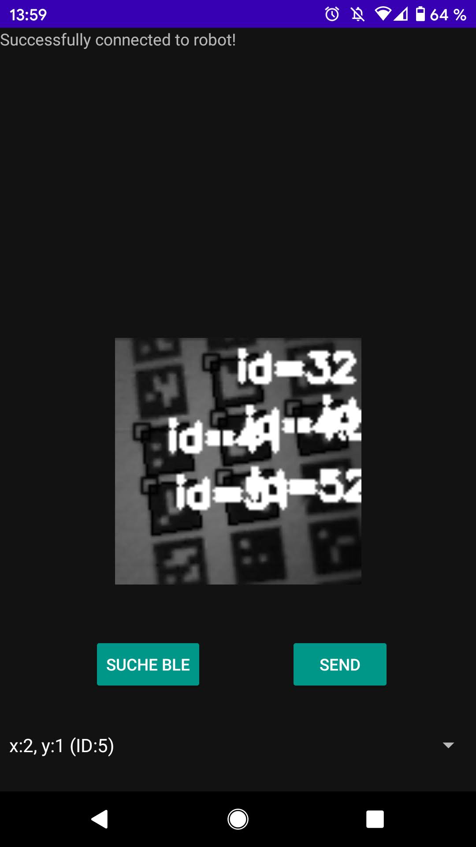
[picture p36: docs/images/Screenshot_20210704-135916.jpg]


## ArUco Board Generation (Python)

PyCharm -> pip install opencv-contrib-python
 ->pip install matplotlib

Das erste Ergebnis ist ein Spielbrett zum Ausdrucken:
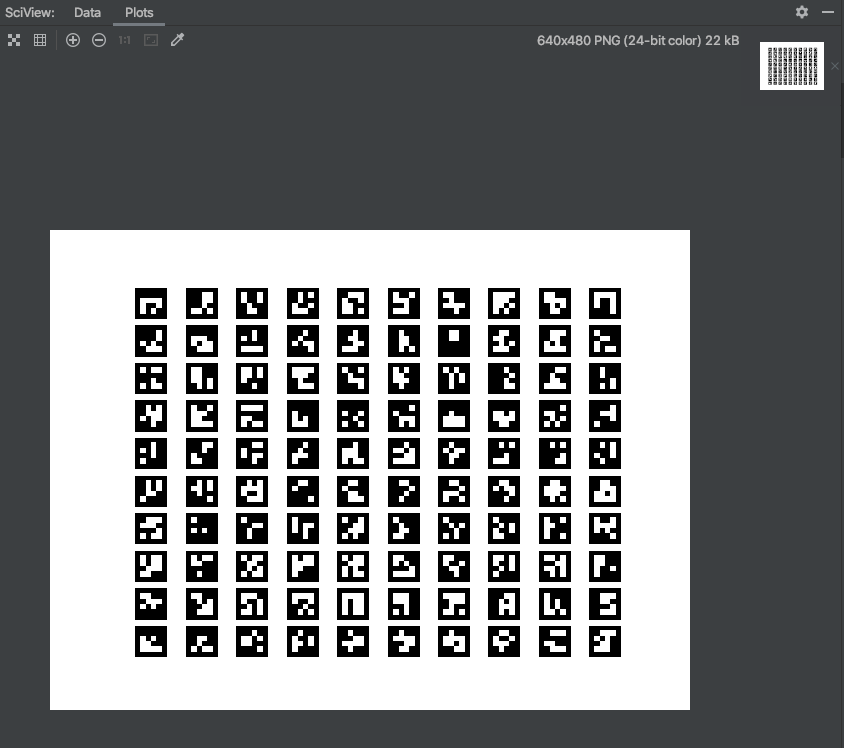
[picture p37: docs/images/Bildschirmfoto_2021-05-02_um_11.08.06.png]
Bildschirmfoto_2021-05-02_um_11.08.06


Am Ende wurde sich für größere Felder (ein Spielfeld ist eine DinA4 Seite groß) und mehr Markern auf den Feldern (50*50 = 2500) entschieden, da die Kamera so nah am Boden ist, dass sie die Marker so am besten erkennt.

Als Beispiel ein 1x2 großes Feld (siehe Bild). Das Feld kann durch ausdrucken weiter Marker bis auf 10x10 vergrößert werden.
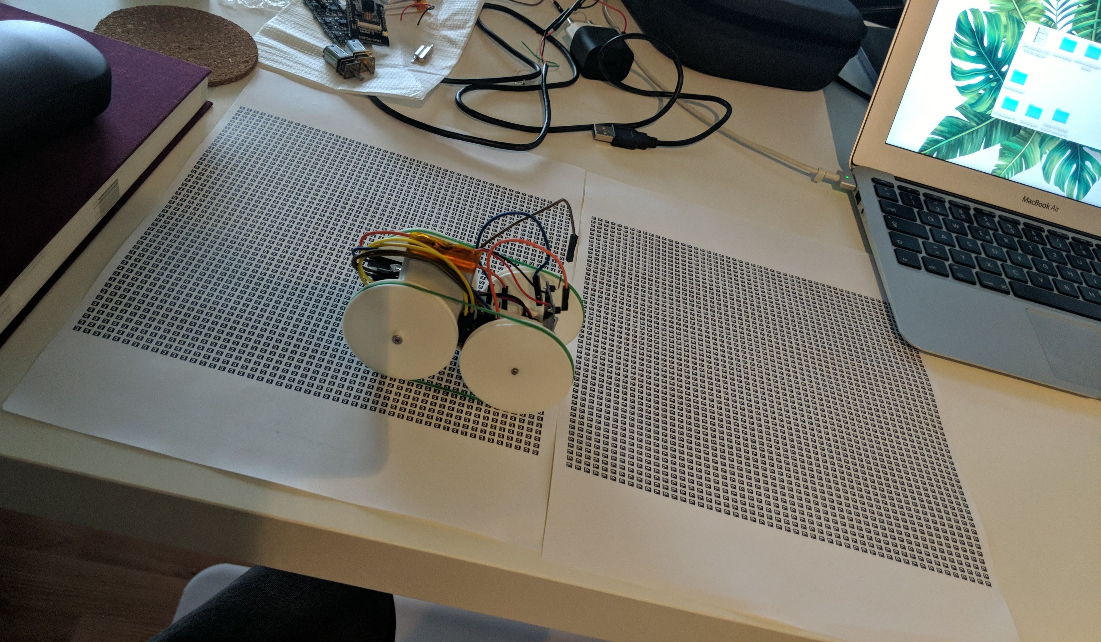
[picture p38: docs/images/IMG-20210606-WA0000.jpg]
IMG-20210606-WA0000


## Ausblick

Ausblick für die Weiterführung des Projekts!

Low Cost für Bürstenmotoren. Diese sind schwerer zu steuern, da man nicht wie bei Schrittmotoren genau weiß, wie viel sie sich bewegen. Das nächste mal also die etwas teureren Schrittmotoren nehmen.

Inferenzen: die Motoren beeinträchtigen die Kamera, dies war vorher auch nicht klar. Es konnte in diesem Projekt gelöst werden, aber man könnte es sich bestimmt noch einfacher machen.

Spielfigur: Der Roboter hat einen ESP32. Eine Spielfigur ist einfach nur eine Figur/Blatt. Diese könnte auch aus einem ESP32 bestehen, ohne Räder, aber mit Kamera, so dass diese auch Marker erkennt und man somit in der App nicht angeben muss, wo die eigene Spielfigur sich befindet, sondern man sie einfach nur setzt. Durch OpenCV und die ArUco Marker Erkennung die wir auch beim Roboter nutzen könnte es somit verbessert werden.

Reifen: Hier benutzen wir Gummibänder, diese springen gelegentlich ab, hier könnte man sich eine andere Konstruktion überlegen, z.B. 3D gedruckte Ketten, wie bei einem Panzer etc..

In der Mitte des Feldes landen: Dies könnte man mit dem Gradientenabstiegsverfahren (Künstliche Intelligenz) machen, indem man ein Feld in der Mitte aus einem ArUco Marker baut, und außen immer in Kreisen drum herum andere Marker setzt, so kennt man die Mitte und kann das Machine Learning Verfahren bzw. den Algorithmus anwenden.

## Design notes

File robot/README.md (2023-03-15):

This is the folder for the code that runs on the robot. The robot is an ESP32-Robot. C++ code with Platformio.

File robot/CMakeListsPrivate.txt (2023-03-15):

# !!! WARNING !!! AUTO-GENERATED FILE, PLEASE DO NOT MODIFY IT AND USE
# https://docs.platformio.org/page/projectconf/section_env_build.html#build-flags
#
# If you need to override existing CMake configuration or add extra,
# please create `CMakeListsUser.txt` in the root of project.
# The `CMakeListsUser.txt` will not be overwritten by PlatformIO.

set(CMAKE_CONFIGURATION_TYPES "esp32cam;native_unit_testing;" CACHE STRING "Build Types reflect PlatformIO Environments" FORCE)

SET(CMAKE_C_COMPILER "$ENV{HOME}/.platformio/packages/toolchain-xtensa32/bin/xtensa-esp32-elf-gcc")
SET(CMAKE_CXX_COMPILER "$ENV{HOME}/.platformio/packages/toolchain-xtensa32/bin/xtensa-esp32-elf-g++")
SET(CMAKE_CXX_FLAGS "-fno-rtti -fno-exceptions -std=gnu++11 -mfix-esp32-psram-cache-issue -Os -g3 -Wall -nostdlib -Wpointer-arith -Wno-error=unused-but-set-variable -Wno-error=unused-variable -mlongcalls -ffunction-sections -fdata-sections -fstrict-volatile-bitfields -Wno-error=deprecated-declarations -Wno-error=unused-function -Wno-unused-parameter -Wno-sign-compare -fstack-protector -fexceptions -Werror=reorder")
SET(CMAKE_C_FLAGS "-std=gnu99 -Wno-old-style-declaration -mfix-esp32-psram-cache-issue -Os -g3 -Wall -nostdlib -Wpointer-arith -Wno-error=unused-but-set-variable -Wno-error=unused-variable -mlongcalls -ffunction-sections -fdata-sections -fstrict-volatile-bitfields -Wno-error=deprecated-declarations -Wno-error=unused-function -Wno-unused-parameter -Wno-sign-compare -fstack-protector -fexceptions -Werror=reorder")

SET(CMAKE_C_STANDARD 99)
set(CMAKE_CXX_STANDARD 11)

if (CMAKE_BUILD_TYPE MATCHES "esp32cam")
    add_definitions(-D'PLATFORMIO=50101')
    add_definitions(-D'ARDUINO_ESP32_DEV')
    add_definitions(-D'BOARD_HAS_PSRAM')
    add_definitions(-D'ESP32')
    add_definitions(-D'ESP_PLATFORM')
    add_definitions(-D'F_CPU=240000000L')
    add_definitions(-D'HAVE_CONFIG_H')
    add_definitions(-D'MBEDTLS_CONFIG_FILE=\"mbedtls/esp_config.h\"')
    add_definitions(-D'ARDUINO=10805')
    add_definitions(-D'ARDUINO_ARCH_ESP32')
    add_definitions(-D'ARDUINO_VARIANT=\"esp32\"')
    add_definitions(-D'ARDUINO_BOARD=\"AI Thinker ESP32-CAM\"')

    include_directories("${CMAKE_CURRENT_LIST_DIR}/include")
    include_directories("${CMAKE_CURRENT_LIST_DIR}/src")
    include_directories("$ENV{HOME}/.platformio/packages/framework-arduinoespressif32/libraries/WiFi/src")
    include_directories("$ENV{HOME}/.platformio/packages/framework-arduinoespressif32/libraries/BluetoothSerial/src")
    include_directories("$ENV{HOME}/.platformio/packages/framework-arduinoespressif32/libraries/BLE/src")
    include_directories("$ENV{HOME}/.platformio/packages/framework-arduinoespressif32/libraries/SD_MMC/src")
    include_directories("$ENV{HOME}/.platformio/packages/framework-arduinoespressif32/libraries/FS/src")
    include_directories("${CMAKE_CURRENT_LIST_DIR}/.pio/libdeps/esp32cam/ESP32 ESP32-S2 AnalogWrite")
    include_directories("${CMAKE_CURRENT_LIST_DIR}/.pio/libdeps/esp32cam/Adafruit SSD1306")
    include_directories("${CMAKE_CURRENT_LIST_DIR}/.pio/libdeps/esp32cam/Adafruit GFX Library")
    include_directories("${CMAKE_CURRENT_LIST_DIR}/.pio/libdeps/esp32cam/Adafruit BusIO")
    include_directories("$ENV{HOME}/.platformio/packages/framework-arduinoespressif32/libraries/SPI/src")
    include_directories("$ENV{HOME}/.platformio/packages/framework-arduinoespressif32/libraries/Wire/src")
    include_directories("$ENV{HOME}/.platformio/packages/framework-arduinoespressif32/tools/sdk/include/config")
    include_directories("$ENV{HOME}/.platformio/packages/framework-arduinoespressif32/tools/sdk/include/app_trace")
    include_directories("$ENV{HOME}/.platformio/packages/framework-arduinoespressif32/tools/sdk/include/app_update")
    include_directories("$ENV{HOME}/.platformio/packages/framework-arduinoespressif32/tools/sdk/include/asio")
    include_directories("$ENV{HOME}/.platformio/packages/framework-arduinoespressif32/tools/sdk/include/bootloader_support")
    include_directories("$ENV{HOME}/.platformio/packages/framework-arduinoespressif32/tools/sdk/include/bt")
    include_directories("$ENV{HOME}/.platformio/packages/framework-arduinoespressif32/tools/sdk/include/coap")
    include_directories("$ENV{HOME}/.platformio/packages/framework-arduinoespressif32/tools/sdk/include/console")
    include_directories("$ENV{HOME}/.platformio/packages/framework-arduinoespressif32/tools/sdk/include/driver")
    include_directories("$ENV{HOME}/.platformio/packages/framework-arduinoespressif32/tools/sdk/include/efuse")
    include_directories("$ENV{HOME}/.platformio/packages/framework-arduinoespressif32/tools/sdk/include/esp-tls")
    include_directories("$ENV{HOME}/.platformio/packages/framework-arduinoespressif32/tools/sdk/include/esp32")
    include_directories("$ENV{HOME}/.platformio/packages/framework-arduinoespressif32/tools/sdk/include/esp_adc_cal")
    include_directories("$ENV{HOME}/.platformio/packages/framework-arduinoespressif32/tools/sdk/include/esp_event")
    include_directories("$ENV{HOME}/.platformio/packages/framework-arduinoespressif32/tools/sdk/include/esp_http_client")
    include_directories("$ENV{HOME}/.platformio/packages/framework-arduinoespressif32/tools/sdk/include/esp_http_server")
    include_directories("$ENV{HOME}/.platformio/packages/framework-arduinoespressif32/tools/sdk/include/esp_https_ota")
    include_directories("$ENV{HOME}/.platformio/packages/framework-arduinoespressif32/tools/sdk/include/esp_https_server")
    include_directories("$ENV{HOME}/.platformio/packages/framework-arduinoespressif32/tools/sdk/include/esp_ringbuf")
    include_directories("$ENV{HOME}/.platformio/packages/framework-arduinoespressif32/tools/sdk/include/esp_websocket_client")
    include_directories("$ENV{HOME}/.platformio/packages/framework-arduinoespressif32/tools/sdk/include/espcoredump")
    include_directories("$ENV{HOME}/.platformio/packages/framework-arduinoespressif32/tools/sdk/include/ethernet")
    include_directories("$ENV{HOME}/.platformio/packages/framework-arduinoespressif32/tools/sdk/include/expat")
    include_directories("$ENV{HOME}/.platformio/packages/framework-arduinoespressif32/tools/sdk/include/fatfs")
    include_directories("$ENV{HOME}/.platformio/packages/framework-arduinoespressif32/tools/sdk/include/freemodbus")
    include_directories("$ENV{HOME}/.platformio/packages/framework-arduinoespressif32/tools/sdk/include/freertos")
    include_directories("$ENV{HOME}/.platformio/packages/framework-arduinoespressif32/tools/sdk/include/heap")
    include_directories("$ENV{HOME}/.platformio/packages/framework-arduinoespressif32/tools/sdk/include/idf_test")
    include_directories("$ENV{HOME}/.platformio/packages/framework-arduinoespressif32/tools/sdk/include/jsmn")
    include_directories("$ENV{HOME}/.platformio/packages/framework-arduinoespressif32/tools/sdk/include/json")
    include_directories("$ENV{HOME}/.platformio/packages/framework-arduinoespressif32/tools/sdk/include/libsodium")
    include_directories("$ENV{HOME}/.platformio/packages/framework-arduinoespressif32/tools/sdk/include/log")
    include_directories("$ENV{HOME}/.platformio/packages/framework-arduinoespressif32/tools/sdk/include/lwip")
    include_directories("$ENV{HOME}/.platformio/packages/framework-arduinoespressif32/tools/sdk/include/mbedtls")
    include_directories("$ENV{HOME}/.platformio/packages/framework-arduinoespressif32/tools/sdk/include/mdns")
    include_directories("$ENV{HOME}/.platformio/packages/framework-arduinoespressif32/tools/sdk/include/micro-ecc")
    include_directories("$ENV{HOME}/.platformio/packages/framework-arduinoespressif32/tools/sdk/include/mqtt")
    include_directories("$ENV{HOME}/.platformio/packages/framework-arduinoespressif32/tools/sdk/include/newlib")
    include_directories("$ENV{HOME}/.platformio/packages/framework-arduinoespressif32/tools/sdk/include/nghttp")
    include_directories("$ENV{HOME}/.platformio/packages/framework-arduinoespressif32/tools/sdk/include/nvs_flash")
    include_directories("$ENV{HOME}/.platformio/packages/framework-arduinoespressif32/tools/sdk/include/openssl")
    include_directories("$ENV{HOME}/.platformio/packages/framework-arduinoespressif32/tools/sdk/include/protobuf-c")
    include_directories("$ENV{HOME}/.platformio/packages/framework-arduinoespressif32/tools/sdk/include/protocomm")
    include_directories("$ENV{HOME}/.platformio/packages/framework-arduinoespressif32/tools/sdk/include/pthread")
    include_directories("$ENV{HOME}/.platformio/packages/framework-arduinoespressif32/tools/sdk/include/sdmmc")
    include_directories("$ENV{HOME}/.platformio/packages/framework-arduinoespressif32/tools/sdk/include/smartconfig_ack")
    include_directories("$ENV{HOME}/.platformio/packages/framework-arduinoespressif32/tools/sdk/include/soc")
    include_directories("$ENV{HOME}/.platformio/packages/framework-arduinoespressif32/tools/sdk/include/spi_flash")
    include_directories("$ENV{HOME}/.platformio/packages/framework-arduinoespressif32/tools/sdk/include/spiffs")
    include_directories("$ENV{HOME}/.platformio/packages/framework-arduinoespressif32/tools/sdk/include/tcp_transport")
    include_directories("$ENV{HOME}/.platformio/packages/framework-arduinoespressif32/tools/sdk/include/tcpip_adapter")
    include_directories("$ENV{HOME}/.platformio/packages/framework-arduinoespressif32/tools/sdk/include/ulp")
    include_directories("$ENV{HOME}/.platformio/packages/framework-arduinoespressif32/tools/sdk/include/unity")
    include_directories("$ENV{HOME}/.platformio/packages/framework-arduinoespressif32/tools/sdk/include/vfs")
    include_directories("$ENV{HOME}/.platformio/packages/framework-arduinoespressif32/tools/sdk/include/wear_levelling")
    include_directories("$ENV{HOME}/.platformio/packages/framework-arduinoespressif32/tools/sdk/include/wifi_provisioning")
    include_directories("$ENV{HOME}/.platformio/packages/framework-arduinoespressif32/tools/sdk/include/wpa_supplicant")
    include_directories("$ENV{HOME}/.platformio/packages/framework-arduinoespressif32/tools/sdk/include/xtensa-debug-module")
    include_directories("$ENV{HOME}/.platformio/packages/framework-arduinoespressif32/tools/sdk/include/esp-face")
    include_directories("$ENV{HOME}/.platformio/packages/framework-arduinoespressif32/tools/sdk/include/esp32-camera")
    include_directories("$ENV{HOME}/.platformio/packages/framework-arduinoespressif32/tools/sdk/include/fb_gfx")
    include_directories("$ENV{HOME}/.platformio/packages/framework-arduinoespressif32/cores/esp32")
    include_directories("$ENV{HOME}/.platformio/packages/framework-arduinoespressif32/variants/esp32")
    include_directories("${CMAKE_CURRENT_LIST_DIR}/.pio/libdeps/esp32cam/ESP32 AnalogWrite/src")
    include_directories("${CMAKE_CURRENT_LIST_DIR}/.pio/libdeps/esp32cam/ESP8266 and ESP32 OLED driver for SSD1306 displays/src")
    include_directories("$ENV{HOME}/.platformio/packages/framework-arduinoespressif32/libraries/ArduinoOTA/src")
    include_directories("$ENV{HOME}/.platformio/packages/framework-arduinoespressif32/libraries/AsyncUDP/src")
    include_directories("$ENV{HOME}/.platformio/packages/framework-arduinoespressif32/libraries/AzureIoT/src")
    include_directories("$ENV{HOME}/.platformio/packages/framework-arduinoespressif32/libraries/DNSServer/src")
    include_directories("$ENV{HOME}/.platformio/packages/framework-arduinoespressif32/libraries/EEPROM/src")
    include_directories("$ENV{HOME}/.platformio/packages/framework-arduinoespressif32/libraries/ESP32/src")
    include_directories("$ENV{HOME}/.platformio/packages/framework-arduinoespressif32/libraries/ESPmDNS/src")
    include_directories("$ENV{HOME}/.platformio/packages/framework-arduinoespressif32/libraries/FFat/src")
    include_directories("$ENV{HOME}/.platformio/packages/framework-arduinoespressif32/libraries/HTTPClient/src")
    include_directories("$ENV{HOME}/.platformio/packages/framework-arduinoespressif32/libraries/HTTPUpdate/src")
    include_directories("$ENV{HOME}/.platformio/packages/framework-arduinoespressif32/libraries/HTTPUpdateServer/src")
    include_directories("$ENV{HOME}/.platformio/packages/framework-arduinoespressif32/libraries/NetBIOS/src")
    include_directories("$ENV{HOME}/.platformio/packages/framework-arduinoespressif32/libraries/Preferences/src")
    include_directories("$ENV{HOME}/.platformio/packages/framework-arduinoespressif32/libraries/SD/src")
    include_directories("$ENV{HOME}/.platformio/packages/framework-arduinoespressif32/libraries/SPIFFS/src")
    include_directories("$ENV{HOME}/.platformio/packages/framework-arduinoespressif32/libraries/SimpleBLE/src")
    include_directories("$ENV{HOME}/.platformio/packages/framework-arduinoespressif32/libraries/Ticker/src")
    include_directories("$ENV{HOME}/.platformio/packages/framework-arduinoespressif32/libraries/Update/src")
    include_directories("$ENV{HOME}/.platformio/packages/framework-arduinoespressif32/libraries/WebServer/src")
    include_directories("$ENV{HOME}/.platformio/packages/framework-arduinoespressif32/libraries/WiFiClientSecure/src")
    include_directories("$ENV{HOME}/.platformio/packages/framework-arduinoespressif32/libraries/WiFiProv/src")
    include_directories("$ENV{HOME}/.platformio/packages/toolchain-xtensa32/xtensa-esp32-elf/include/c++/5.2.0")
    include_directories("$ENV{HOME}/.platformio/packages/toolchain-xtensa32/xtensa-esp32-elf/include/c++/5.2.0/xtensa-esp32-elf")
    include_directories("$ENV{HOME}/.platformio/packages/toolchain-xtensa32/lib/gcc/xtensa-esp32-elf/5.2.0/include")
    include_directories("$ENV{HOME}/.platformio/packages/toolchain-xtensa32/lib/gcc/xtensa-esp32-elf/5.2.0/include-fixed")
    include_directories("$ENV{HOME}/.platformio/packages/toolchain-xtensa32/xtensa-esp32-elf/include")
    include_directories("$ENV{HOME}/.platformio/packages/tool-unity")

    FILE(GLOB_RECURSE EXTRA_LIB_SOURCES
        ${CMAKE_CURRENT_LIST_DIR}/.pio/libdeps/esp32cam/*.*
    )
endif()

if (CMAKE_BUILD_TYPE MATCHES "native_unit_testing")
    add_definitions(-D'PLATFORMIO=50101')

    include_directories("${CMAKE_CURRENT_LIST_DIR}/include")
    include_directories("${CMAKE_CURRENT_LIST_DIR}/src")
    include_directories("$ENV{HOME}/.platformio/packages/tool-unity")

    FILE(GLOB_RECURSE EXTRA_LIB_SOURCES
        ${CMAKE_CURRENT_LIST_DIR}/.pio/libdeps/native_unit_testing/*.*
    )
endif()

FILE(GLOB_RECURSE SRC_LIST
    ${CMAKE_CURRENT_LIST_DIR}/src/*.*
    ${CMAKE_CURRENT_LIST_DIR}/lib/*.*
)

list(APPEND SRC_LIST ${EXTRA_LIB_SOURCES})

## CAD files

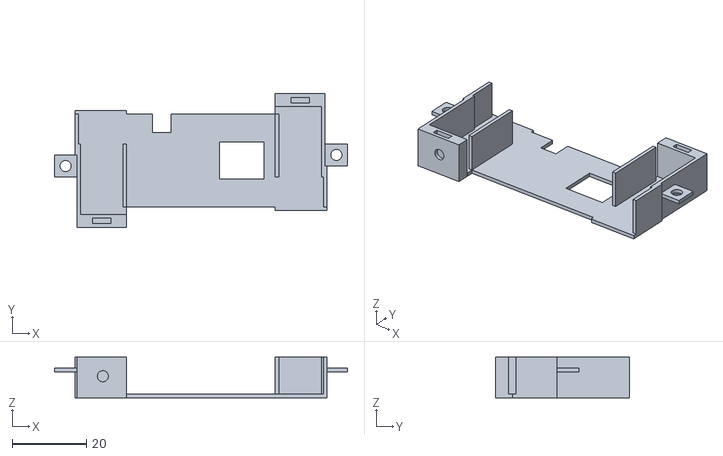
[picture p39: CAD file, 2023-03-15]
docs/CAD/unteres Gestell.stl
79.0 x 36.0 x 11.0

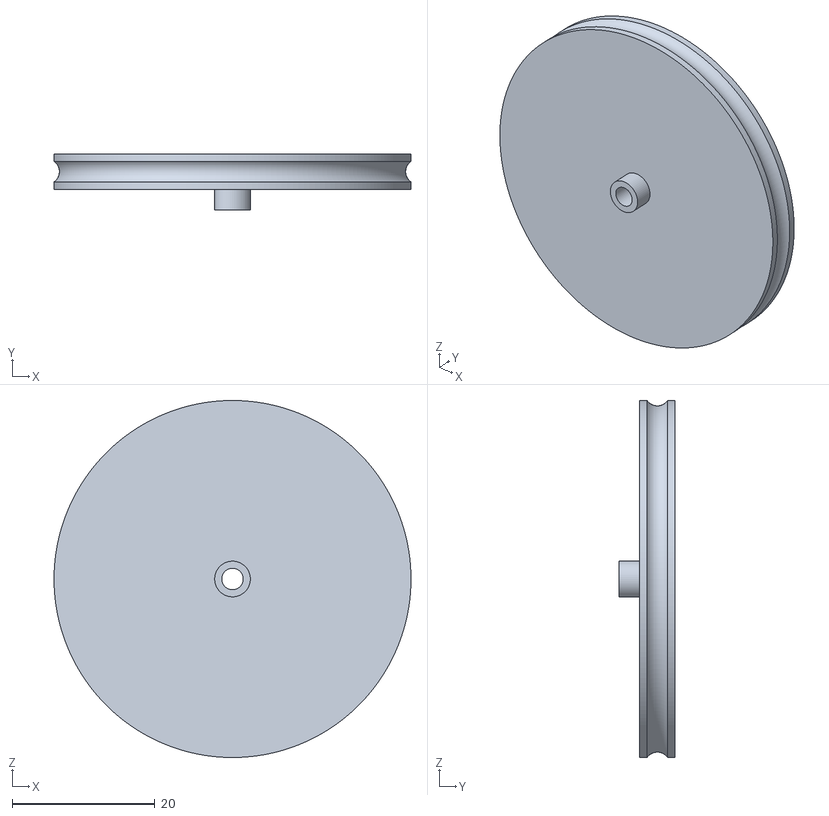
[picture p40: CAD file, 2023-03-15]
docs/CAD/Reifen.stl
50.0 x 7.90 x 50.0

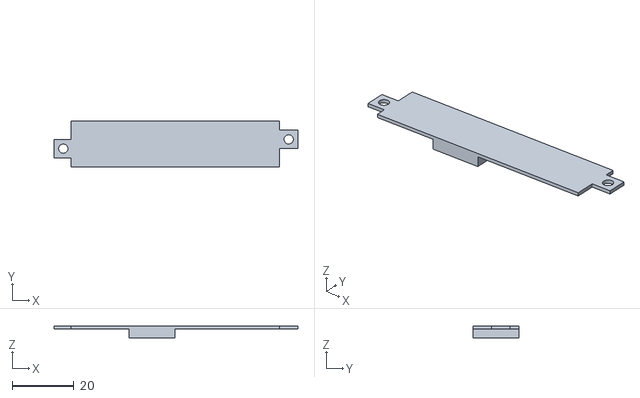
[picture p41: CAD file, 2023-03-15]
docs/CAD/oberes Gestell.stl
79.0 x 15.0 x 4.00

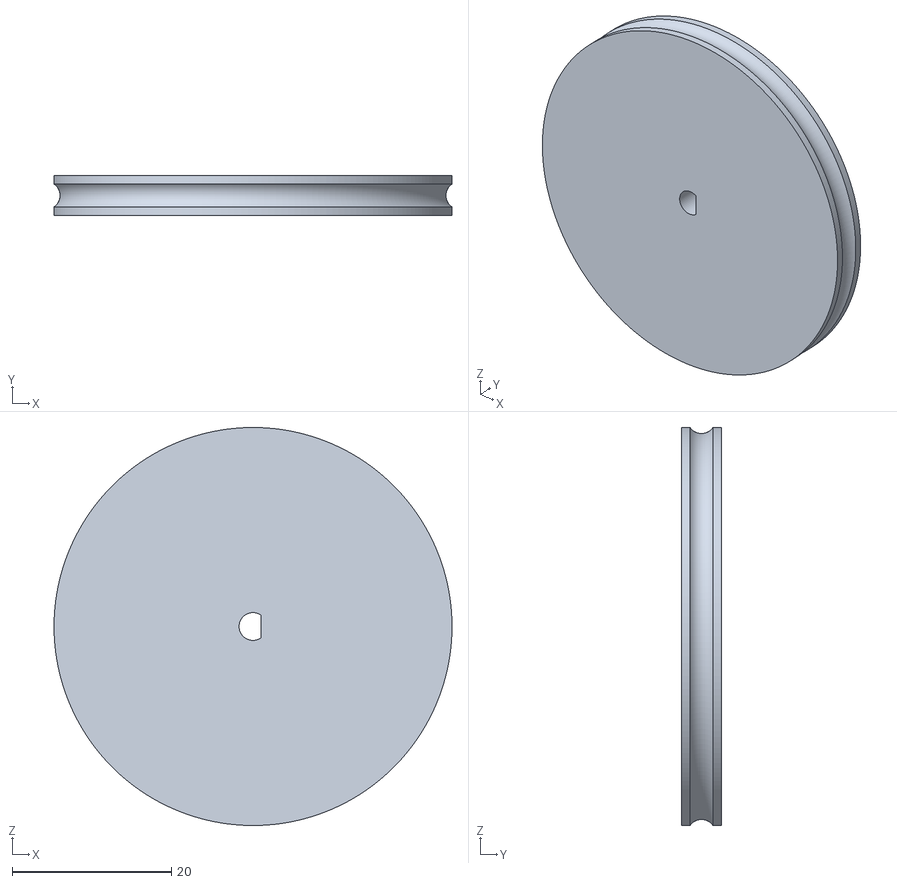
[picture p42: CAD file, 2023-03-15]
docs/CAD/ReifenMotor.stl
50.0 x 5.00 x 50.0

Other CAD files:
docs/CAD/SoftwareProjekt.f3d

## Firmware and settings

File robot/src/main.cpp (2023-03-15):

#ifndef UNIT_TEST //this means, this class is not for unit testing, because of arduino specific stuff

#include <Arduino.h>
#include <iostream>

#include "hal/communication.h"
#include "hal/motor.h"
#include "hal/display.h"
#include "hal/dummy_display.h"
#include "hal/camera.h"
#include "image_preprocessing.h"
#include "dispatcher.h"

#define MOTOR1_PIN1 2
#define MOTOR1_PIN2 14
#define MOTOR2_PIN1 13
#define MOTOR2_PIN2 12

static dispatcher *test_disp;

void setup() __attribute__((noreturn));
void setup() {
    Serial.begin(115200);
    delay(2000);

    std::cout << "Starting!" << std::endl;

    communication test_obj = communication();

    motor test_motor = motor(MOTOR1_PIN1, MOTOR1_PIN2, LEDC_CHANNEL_4, LEDC_CHANNEL_5);
    motor test_motor2 = motor(MOTOR2_PIN1, MOTOR2_PIN2, LEDC_CHANNEL_6, LEDC_CHANNEL_7);
    dummy_display test_display;
    camera test_camera = camera();
    image_preprocessing prepro(test_camera);
    test_disp = new dispatcher{prepro, test_motor, test_motor2, test_display, test_obj};
    communication::message_callback_t callback = [](std::string message){test_disp->callback(message);};
    test_obj.bind_callback_bluetooth(callback);

    while(true) {
        test_disp->dispatch();
        delay(100); //to avoid to much traffic (backpressure)
        //test_display.update();
    }
}

void loop() {

}

#endif

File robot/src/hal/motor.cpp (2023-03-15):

//
// Created by Lea Wü on 28.03.21.
//
#ifndef UNIT_TEST

#include "hal/motor.h"

//Constructor
motor::motor(int pin1, int pin2, int pwmChannel1, int pwmChannel2) {
    this->pin1 = pin1;
    this->pin2 = pin2;
    this->pwmChannel1 = pwmChannel1;
    this->pwmChannel2 = pwmChannel2;

    pinMode(pin1, OUTPUT);
    pinMode(pin2, OUTPUT);

    ledcSetup(pwmChannel1, 100, 8);
    ledcSetup(pwmChannel2, 100, 8);

    ledcAttachPin(pin1, pwmChannel1);
    ledcAttachPin(pin2, pwmChannel2);

    //timer for the overloaded start function
    esp_timer_create_args_t oneshot_timer_args;
    oneshot_timer_args.callback = [](void *motor_p) {
        ((motor *) motor_p)->stop();
    };
    /* argument specified here will be passed to timer callback function */
    oneshot_timer_args.arg = (void *) (this);
    oneshot_timer_args.name = (String("motor") + String(pwmChannel1)).c_str();
    ESP_ERROR_CHECK(esp_timer_create(&oneshot_timer_args, &timer));
}

//Destructor
motor::~motor() {
    ESP_ERROR_CHECK(esp_timer_delete(timer));
}

void motor::start(bool forward, uint8_t speed) {
    if (forward) {
        ledcWrite(pwmChannel1, 0);
        ledcWrite(pwmChannel2, speed);
    } else { //backwards
        ledcWrite(pwmChannel2, 0);
        ledcWrite(pwmChannel1, speed);
    }
}

//overloaded function
void motor::start(bool forward, uint8_t speed, uint16_t time) {
    if (forward) {
        ledcWrite(pwmChannel1, 0);
        ledcWrite(pwmChannel2, speed);
    } else { //backwards
        ledcWrite(pwmChannel2, 0);
        ledcWrite(pwmChannel1, speed);
    }

    ESP_ERROR_CHECK(esp_timer_start_once(timer, time * 1000)); //milliseconds
}

void motor::stop() {
    ledcWrite(pwmChannel1, 0);
    ledcWrite(pwmChannel2, 0);
}

#endif

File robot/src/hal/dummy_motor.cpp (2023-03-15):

//
// Created by Lea Wü on 28.03.21.
//

#include <iostream>
#include "hal/dummy_motor.h"

//this dummy_motor is for testing without real motor

//Constructor
dummy_motor::dummy_motor() {

}

//Destructor
dummy_motor::~dummy_motor() {

}

void dummy_motor::start(bool forward, uint8_t speed) {
    if(forward){
        std::cout << "[This is the Motor simulation:] The motor started and the robot is moving forward" << std::endl;
    } else{ //backwards
        std::cout << "[This is the Motor simulation:] The motor started and the robot is moving backwards" << std::endl;
    }

}

void dummy_motor::start(bool forward, uint8_t speed, uint16_t time) {
    if(forward){
        std::cout << "[This is the Motor simulation:] The motor started and the robot is moving forward" << std::endl;
    } else{ //backwards
        std::cout << "[This is the Motor simulation:] The motor started and the robot is moving backwards" << std::endl;
    }

}

void dummy_motor::stop() {
    std::cout << "[This is the Motor simulation:] The motor stopped and the robot isn't moving any more" << std::endl;
}
